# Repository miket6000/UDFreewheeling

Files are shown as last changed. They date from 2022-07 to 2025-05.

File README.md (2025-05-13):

# UDFreewheeling
A Freewheeling DRSSTC controller based loosely on the UD2.7. See it running my 35cm coil here: (https://youtu.be/EUlrq9CbajI)

Follow the development history at https://highvoltageforum.net/index.php?topic=2054.0

The driver behind building a new Tesla Coil Controller was to create something as simple to build and use as the UD2.7 (https://loneoceans.com/labs/ud27/) but with the below improvements:
* Freewheeling over current protection, this limits the maximum current without terminating the burst
* Over current and current phase detected with a single current transformer (CT)
* Removed the need for difficult to obtain variable inductors
* Self oscillating for improved startup at lower feedback currents

There are a couple of breaking changes that are worth pointing out:
* While the board outline is approximately the same as UD2.7 I can't guarantee the mounting holes are in the exact same locations
* There is no longer the ability to disable phase lead, it wasn't obvious why this would be required and can be done by using a short instead of L1
* The location of the HFBR is approximately the same as the UD2.7 but the location of the IF-D95 has changed slightly

Huge thanks to the assistance of all those at highvoltageforum.net and especially David Knierim for his extensive contributions.

## How it works
### Power supply
There's nothing much here to talk about, there are three regulators, 24V, 9V and 5V. 24V and 5V are linear, the 9V should be a DC/DC converter such as  RECOM Power R-78E9.0-0.5 or similar. It is recommended for the input supply that you use a 1A 24V SMPS and the DC input. Do not use the DC and AC inputs at the same time.

### Phase detect
The CT should be designed to provide a current of ~500mA to 1A peak at maximum primary current.
C32 provides HF bypass for noise. The current from the CT passes through R3 || R8 L1 and R1 generating a voltage ton pin 1 of R8 hat leads the current by theta = arctan(Xl / R). Xl depends on the operating frequency of the primary but R just depends on the position of the wiper on R8 and can be set from 5.1R up to R3 || R9 which is approximately 22R. This voltage is then clamped to +/- 0.65V by the back to back diodes and capacitvely coupled into the inverting input of the comparator IC8.

IC8 is set up with both positive and negative feedback with the non-inverting input held at nominally 2.5V. If we initially ignore any input from the CT we can see that the comparator will attempt to pull the inverting input low. There will be a time constant set by C5 and (R21 + R25) which will mean this takes some amount of time but the voltage at the input will be reducing. Meanwhile when the input transitioned low C33, R26 and R7 immediately pulled the non-inverting input low but C33 will slowly charge so the voltage at the non-inverting input will be increasing.

After some amount of time the increasing voltage on the non-inverting input and the decreasing voltage in the inverting input will be equal and the pass each other. At this moment the comparator will toggle states at the output will go high. This will reverse our initial state and everything happens again, but with the voltages reversed, i.e. it oscillates. The oscillation frequency can be set by adjusting R25. This should be set as close as possible to the frequency of the primary. To set the correct frequency ensure there is no feedback from the CT (i.e. disconnect the output stage or the CT) and measure the frequency on an oscilloscope. Adjust R25 until this matches your expected resonant frequency.

When there is a signal from the CT it swamps the ability of the negative feedback from R21 + R25 to control the inverting input pin so is effectively overriden with the natural resonant frequency of the system.

### Over current detection
The current through the CT creates a voltage across R1 (5R1). This is clamped between the 0V and 5V rails and feed into the inverting input of U5A. If the voltage exceeds the voltage set by R20 then the output of the comparator will go low signaling an over current event to the logic controlling the gate drivers. The over current threshold is determined by taking your intended over current peak, dividing it by the CT ratio and multiplying by 5.1V. R20 is then adjusted until this voltage is measured on TP6. E.G. I have a 300:1 CT and want the over current limit to be set to 200A, so I adjust R20 until I see 200A / 300 * 5.1V = 3.4V.

### Interrupt input
A signal present on the optical input of RX1 (active low) is inverted by IC4F so that the output is high when the signal is present (LED on). A signal present on the optical input of RX2 (active high) is first inverted and the pulls down the same node as RX1 which is then inverted again so that the output is again high when the signal is present. The two RX inputs are effectively OR'd together so it is not recommended to use both inputs at the same time. If RX2 is not placed it is necessary to either tie the input of IC4B low (by shorting RX2-RX1) or remove D12. Note, if you do decide to remove D12 it is still necessary to include R11 to prevent oscillation caused by a floating input to IC4B.

### Undervoltage Lockout (UVLO)
The under voltage lockout compares the 24V rail (divided by 6 and applied to the non-inverting input of U5B) to the reference voltage set by R27 applied to the inverting input of U5B. If the voltage drops below the reference voltage the output goes low signaling to the gate drive logic that an undervoltage has occured. The reference is set by dividing your desired UVLO voltage by 6 and adjusting R27 until you see the desired voltage on TP4. E.G. I want UVLO to trigger at 18V, 18V / 6 = 3V so I adjust R27 until I measure 3V on TP4.

### Gate drivers
This is borrowed directly from UD2.7C, the two UCC27423 dual inverting gate drivers are used to drive two FDD8424H complementry MOSFETs to run the gate drive transformers. The only difference is that there are seperate signals for the two GDTs. This means it is not possible to parallel the twou outputs, each needs to run its own GDT, one for each half of the full bridge. 

### Gate drive logic
This is the complex part. We'll start at the gate drivers and move backwards...
IC12 is a multiplexer. It has two sets of 4 inputs and will take one of the two sets of inputs and connect them to the outputs. The schematic uses a slightly different nomenclature than the datasheet but for each pair of input pins ('I0a' & 'I1a' are one pair) if the 'S' pin is low then the voltage at input 'I0a' is connected to output 'Za', if the 'S' pin is high then the voltage at 'I1a' is connected to 'Za'. All the pairs are switched at the same time. This is all assuming the Enable (E) pin is low, otherwise the outputs are all low.

We connect CLK to our 'S' pin. Looking at the 'a' and 'b' inputs which connect to GDT1 we can see that 'Za' and 'Zb' have complementy outputs, if 'Za' is high, 'Zb' is low and vice-verse. CLK is derived from our phase signal so always drives GDT1 in phase with the phase signal. Inputs 'c' and 'd' are more complex. They are driven by the putpus of IC6B so depending on the state of IC6B could be either driven in phase or out of phase with CLK. If they're driven in phase with CLK (i.e. 'Q' is high) then both sides of the H-bridge will be in phase with each other and there will be no voltage across the primary tank circuit, i.e. we're freewheeling. The currents in the LC circuit are free to slosh backwards and forwards without significant resistance from the bridge. If however 'Q' is low then the output to GDT2 is out of phase and the HVDC bus voltage will occure across the primary tank causing it to ring up.

IC6B samples IC6A's 'Qn' output and latches it for the next clock cycle on every rising 'CLK' edge. Under "normal" circumstances IC6A clocks in 5V on the 'D' pin so 'Qn' is 0V. 0V on the 'D' pin of IC6B means the drive is out of phase and we ring up the current. If however OCD is asserted low by the over current detect comparator at any stage during the clock cycle the output of IC6B's 'Qn' output will go high. It will stay high until the next clock edge samples the 'D' input and drives 'Qn' low again, but going low takes time, before that happens the state has already been samples by IC6B and locked in for the next cycle. The INTERRUPT signal on the 'set' pin just ensures that we're in the correct state (freewheeling off) in between on signals from the interrupter, otherwise we wouldn't be able to start.

IC5A will disable the output of IC12 whenever INTERRUPT is low and there is a rising edge on the CLK signal. It can also disable IC12 if its 'R' line is asserted low by IC5B which is used to latch the UVLO signal. This means that if the UVLO is triggered then the output will remain locked out until the next rising edge of INTERRUPT.

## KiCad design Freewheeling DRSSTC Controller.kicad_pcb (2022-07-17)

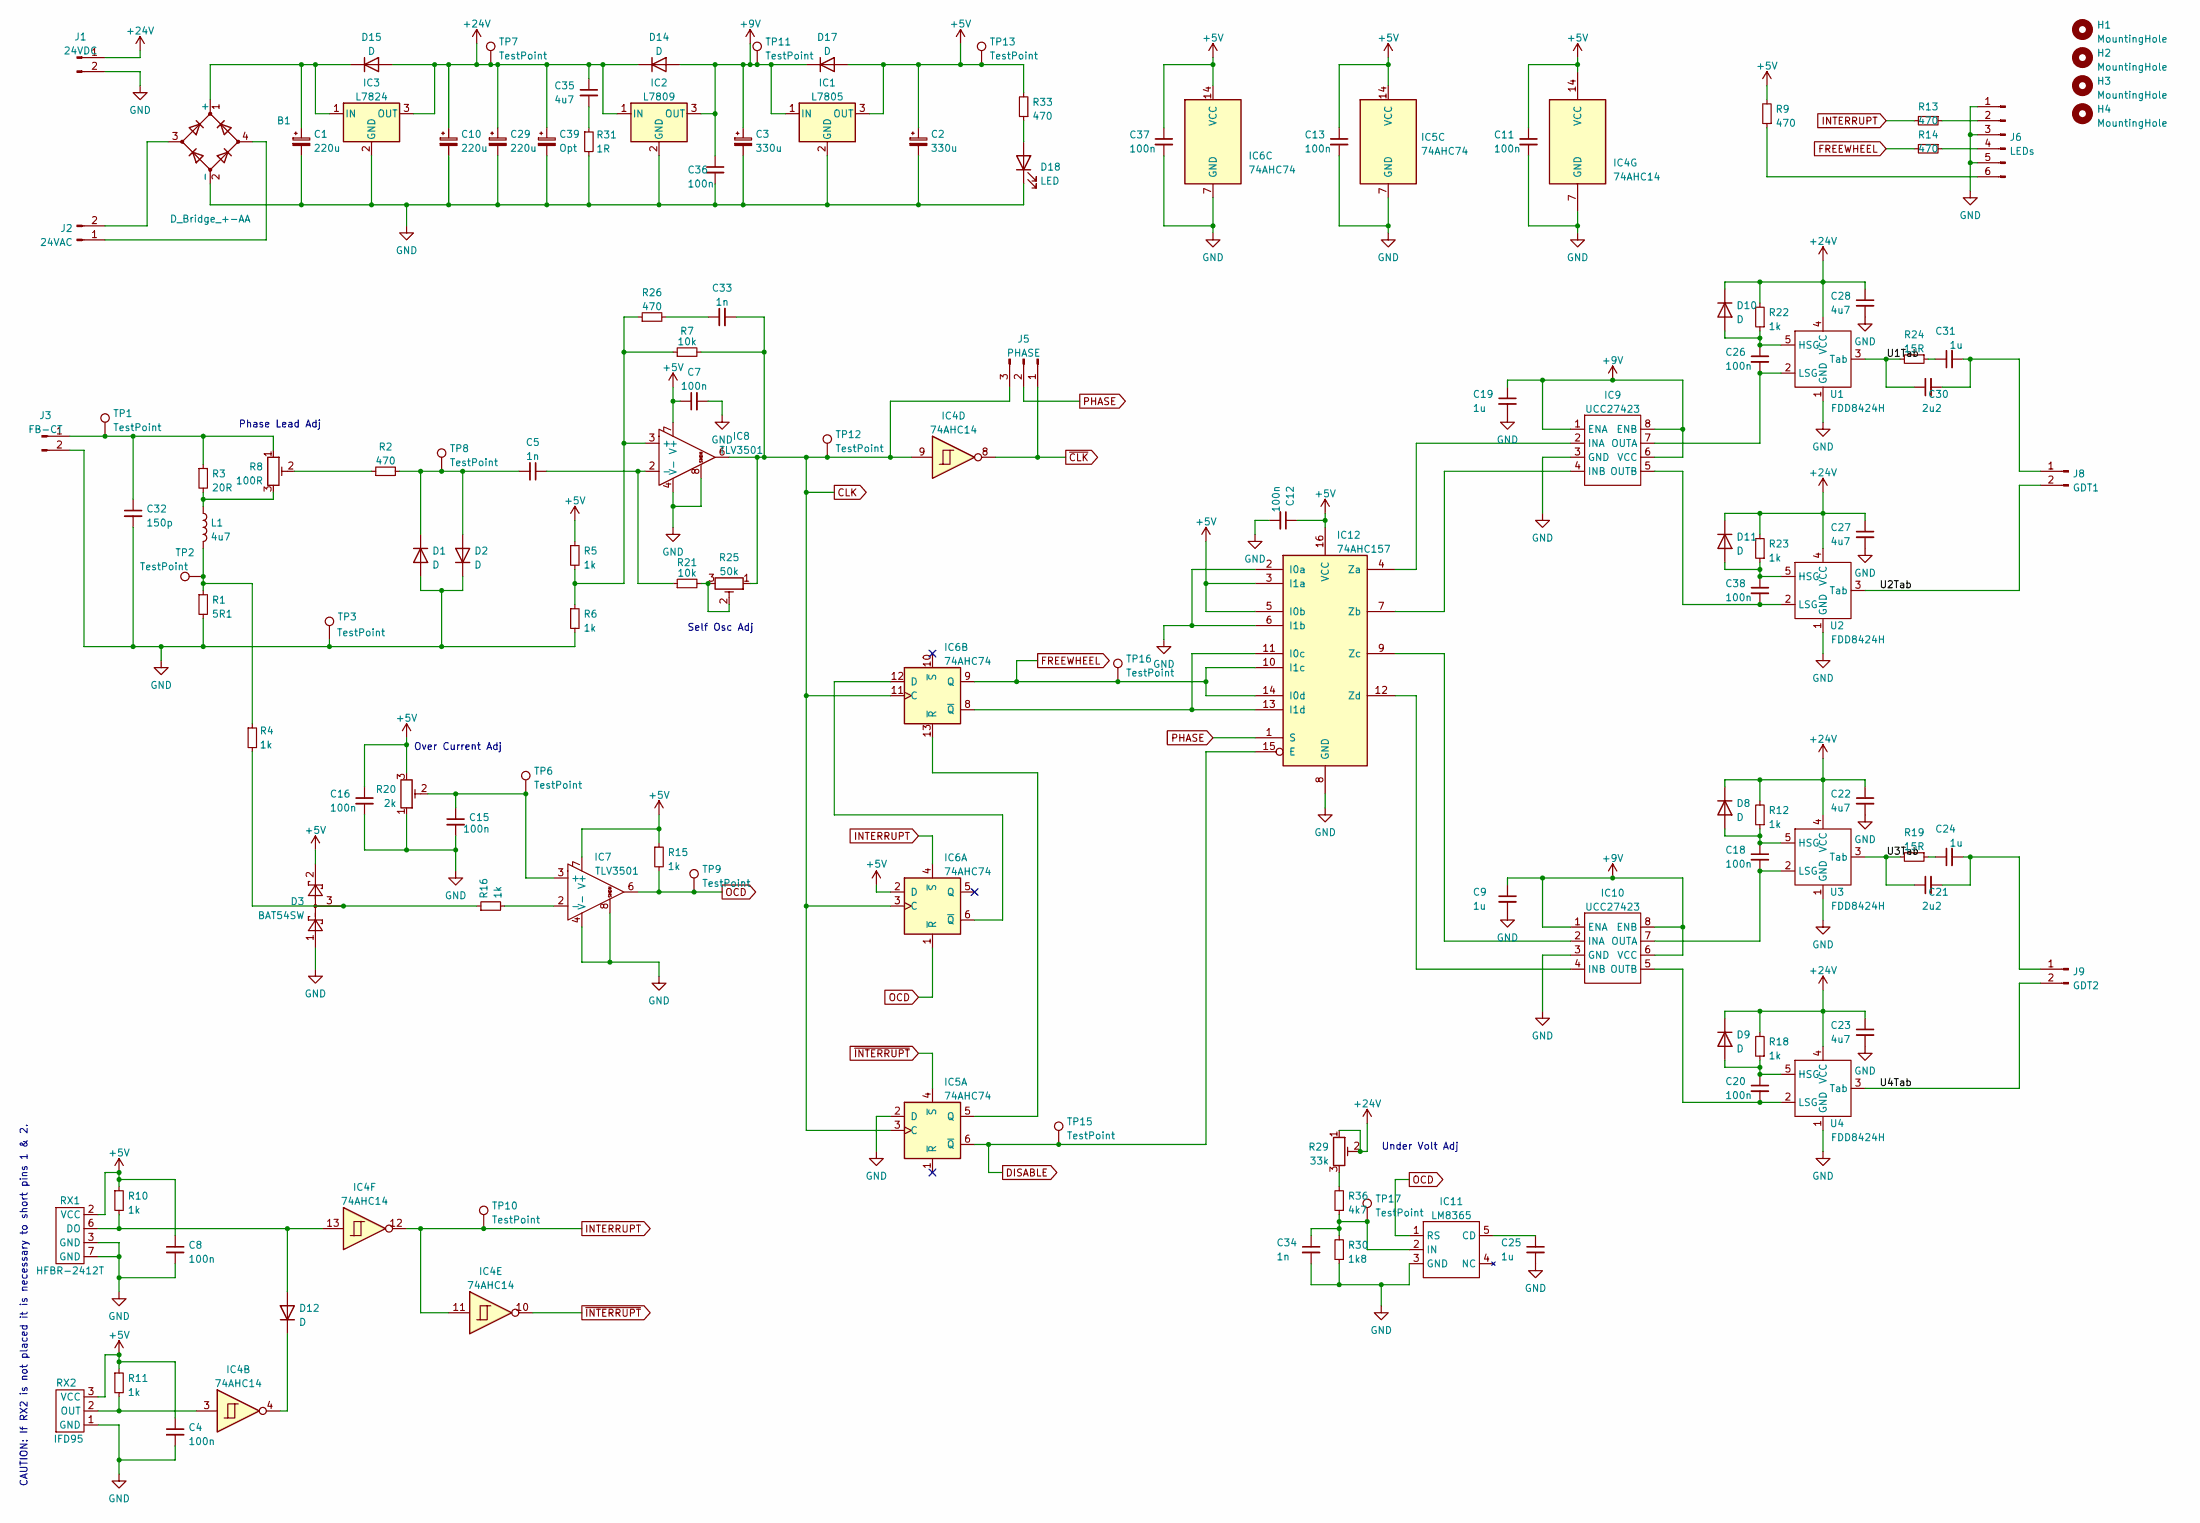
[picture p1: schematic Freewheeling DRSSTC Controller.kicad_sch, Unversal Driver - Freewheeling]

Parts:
B1: D_Bridge_+-AA; Diode_Bridge_Vishay_DFS
C1, C10, C29: 220u; CP_Radial_D8.0mm_P3.50mm
C2, C3: 330u; CP_Radial_D8.0mm_P3.50mm
C4, C7, C8, C11, C12, C13, C15, C16, C18, C20, C26, C36, C37, C38: 100n; C_0805_2012Metric
C5, C33, C34: 1n; C_0805_2012Metric
C9, C19, C25: 1u; C_0805_2012Metric
C21, C30: 2u2; C_1210_3225Metric
C22, C23, C27, C28, C35: 4u7; C_1206_3216Metric
C24, C31: 1u; C_1206_3216Metric
C32: 150p; C_0805_2012Metric
C39: Opt; CP_Radial_D8.0mm_P3.50mm
D1, D2, D14, D15, D17: D; D_SOD-123
D3: BAT54SW; SOT-23
D8, D9, D10, D11, D12: D; D_SOD-323
D18: LED; D_0805_2012Metric
H1, H2, H3, H4: MountingHole; MountingHole_3.2mm_M3
IC1: L7805; TO-252-3_TabPin2
IC2: L7809; TO-220-3_Vertical
IC3: L7824; TO-263-2
IC4: 74AHC14; SOIC-14_3.9x8.7mm_P1.27mm
IC5, IC6: 74AHC74; SOIC-14_3.9x8.7mm_P1.27mm
IC7, IC8: TLV3501; SOIC-8_3.9x4.9mm_P1.27mm
IC9, IC10: UCC27423; SOIC-8_3.9x4.9mm_P1.27mm
IC11: LM8365; SOT-23-5
IC12: 74AHC157; SOIC-16_3.9x9.9mm_P1.27mm
J1: 24VDC; JST_XH_B2B-XH-A_1x02_P2.50mm_Vertical
J2: 24VAC; JST_XH_B2B-XH-A_1x02_P2.50mm_Vertical
J3: FB-CT; JST_XH_B2B-XH-A_1x02_P2.50mm_Vertical
J5: PHASE; PinHeader_1x03_P2.54mm_Vertical
J6: LEDs; PinHeader_1x06_P2.54mm_Vertical
J8: GDT1; JST_XH_B2B-XH-A_1x02_P2.50mm_Vertical
J9: GDT2; JST_XH_B2B-XH-A_1x02_P2.50mm_Vertical
L1: 4u7; L_Axial_L11.0mm_D4.5mm_P5.08mm_Vertical_Fastron_MECC
R1: 5R1; R_Axial_DIN0414_L11.9mm_D4.5mm_P15.24mm_Horizontal
R2, R9, R13, R14, R26, R33: 470; R_0805_2012Metric
R3: 20R; R_Axial_DIN0414_L11.9mm_D4.5mm_P15.24mm_Horizontal
R4, R5, R6, R10, R11, R12, R15, R16, R18, R22, R23: 1k; R_0805_2012Metric
R7, R21: 10k; R_0805_2012Metric
R8: 100R; Potentiometer_Bourns_3296W_Vertical
R19, R24: 15R; R_1210_3225Metric
R20: 2k; Potentiometer_Bourns_3296W_Vertical
R25: 50k; Potentiometer_Bourns_3296W_Vertical
R29: 33k; Potentiometer_Bourns_TC33X_Vertical
R30: 1k8; R_0805_2012Metric
R31: 1R; R_0805_2012Metric
R36: 4k7; R_0805_2012Metric
RX1: HFBR-2412T; HFBR-x41x
RX2: IFD95; IF-D95
TP1, TP2, TP3, TP6, TP7, TP8, TP9, TP10, TP11, TP12, TP13, TP15, TP16, TP17: TestPoint; TestPoint_THTPad_D1.0mm_Drill0.5mm
U1, U2, U3, U4: FDD8424H; TO-252-4

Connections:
+5V: C2.1, C4.1, C7.1, C8.1, C11.1, C12.1, C13.1, C16.1, C37.1, D3.2, D17.2 (A), IC1.3 (OUT), IC4.14 (VCC), IC5.14 (VCC), IC6.2 (D), IC6.14 (VCC), IC7.7 (V+), IC8.7 (V+), IC12.3 (I1a), IC12.5 (I0b), IC12.16 (VCC), R5.1, R9.2, R10.1, R11.1, R15.1, R20.3, R33.2, RX1.2 (VCC), RX2.3 (VCC), TP13.1
+9V: C3.1, C9.1, C19.1, C36.1, D14.2 (A), D17.1 (K), IC1.1 (IN), IC2.3 (OUT), IC9.1 (ENA), IC9.6 (VCC), IC9.8 (ENB), IC10.1 (ENA), IC10.6 (VCC), IC10.8 (ENB), TP11.1
+24V: C10.1, C22.1, C23.1, C27.1, C28.1, C29.1, C35.1, C39.1, D8.1 (K), D9.1 (K), D10.1 (K), D11.1 (K), D14.1 (K), D15.2 (A), IC2.1 (IN), IC3.3 (OUT), J1.1, R12.2, R18.2, R22.2, R23.2, R29.1, R29.2, TP7.1, U1.4 (VCC), U2.4 (VCC), U3.4 (VCC), U4.4 (VCC)
/U1Tab: C30.1, R24.2, U1.3 (Tab)
/U2Tab: J8.2, U2.3 (Tab)
/U3Tab: C21.1, R19.2, U3.3 (Tab)
/U4Tab: J9.2, U4.3 (Tab)
CLK: C33.2, IC4.9, IC5.3 (C), IC6.3 (C), IC6.11 (C), IC8.6, J5.3, R7.2, R25.1, TP12.1
DISABLE: IC5.6 (~Q), IC12.15 (E), TP15.1
FREEWHEEL: IC6.9 (Q), IC12.10 (I1c), IC12.14 (I0d), R14.2, TP16.1
GND: B1.2 (-), C1.2, C2.2, C3.2, C4.2, C7.2, C8.2, C9.2, C10.2, C11.2, C12.2, C13.2, C15.2, C16.2, C19.2, C22.2, C23.2, C25.2, C27.2, C28.2, C29.2, C32.2, C34.2, C36.2, C37.2, C39.2, D1.2 (A), D2.1 (K), D3.1, D18.1 (K), IC1.2 (GND), IC2.2 (GND), IC3.2 (GND), IC4.7 (GND), IC5.2 (D), IC5.7 (GND), IC6.7 (GND), IC7.4 (V-), IC7.8, IC8.4 (V-), IC8.8, IC9.3 (GND), IC10.3 (GND), IC11.3 (GND), IC12.2 (I0a), IC12.6 (I1b), IC12.8 (GND), J1.2, J3.2, J6.1, J6.3, J6.5, R1.2, R6.2, R20.1, R30.1, R31.2, RX1.3 (GND), RX1.7 (GND), RX2.1 (GND), TP3.1, U1.1 (GND), U2.1 (GND), U3.1 (GND), U4.1 (GND)
INTERRUPT: IC4.11, IC4.12, IC6.4 (~S), R13.2, TP10.1
unnamed: B1.1 (+), C1.1, D15.1 (K), IC3.1 (IN)
unnamed: B1.3, J2.2
unnamed: B1.4, J2.1
unnamed: C18.1, D8.2 (A), R12.1, U3.5 (HSG)
unnamed: C18.2, IC10.7 (OUTA), U3.2 (LSG)
unnamed: C20.1, D9.2 (A), R18.1, U4.5 (HSG)
unnamed: C20.2, IC10.5 (OUTB), U4.2 (LSG)
unnamed: C21.2, C24.2, J9.1
unnamed: C24.1, R19.1
unnamed: C25.1, IC11.5 (CD)
unnamed: C26.1, D10.2 (A), R22.1, U1.5 (HSG)
unnamed: C26.2, IC9.7 (OUTA), U1.2 (LSG)
unnamed: C30.2, C31.2, J8.1
unnamed: C31.1, R24.1
unnamed: C33.1, R26.2
unnamed: C34.1, IC11.2 (IN), R30.2, R36.1, TP17.1
unnamed: C35.2, R31.1
unnamed: C38.1, D11.2 (A), R23.1, U2.5 (HSG)
unnamed: C38.2, IC9.5 (OUTB), U2.2 (LSG)
unnamed: C5.2, D1.1 (K), D2.2 (A), R2.2, TP8.1
unnamed: D12.1 (K), IC4.4
unnamed: D12.2 (A), IC4.13, R10.2, RX1.6 (DO)
unnamed: D18.2 (A), R33.1
unnamed: IC4.3, R11.2, RX2.2 (OUT)
unnamed: IC6.8 (~Q), IC12.11 (I0c), IC12.13 (I1d)
unnamed: IC6.6 (~Q), IC6.12 (D)
unnamed: IC5.5 (Q), IC6.13 (~R)
unnamed: IC7.2 (-), R16.2
unnamed: C5.1, IC8.2 (-), R21.1
unnamed: IC9.2 (INA), IC12.4 (Za)
unnamed: IC9.4 (INB), IC12.7 (Zb)
unnamed: IC10.2 (INA), IC12.9 (Zc)
unnamed: IC10.4 (INB), IC12.12 (Zd)
unnamed: J6.2, R13.1
unnamed: J6.4, R14.1
unnamed: J6.6, R9.1
unnamed: L1.1, R3.2, R8.3
unnamed: L1.2, R1.1, R4.1, TP2.1
unnamed: C32.1, J3.1, R3.1, R8.1, TP1.1
unnamed: R2.1, R8.2
unnamed: D3.3, R4.2, R16.1
unnamed: C15.1, IC7.3 (+), R20.2, TP6.1
unnamed: R21.2, R25.2, R25.3
unnamed: IC8.3 (+), R5.2, R6.1, R7.1, R26.1
unnamed: R29.3, R36.2
OCD: IC6.1 (~R), IC7.6, IC11.1 (RS), R15.2, TP9.1
PHASE: IC12.1 (S), J5.2
~CLK: IC4.8, J5.1
~INTERRUPT: IC4.10, IC5.4 (~S)

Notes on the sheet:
CAUTION: If RX2 is not placed it is necessary to short pins 1 & 2.
Over Current Adj
Under Volt Adj
Self Osc Adj
Phase Lead Adj

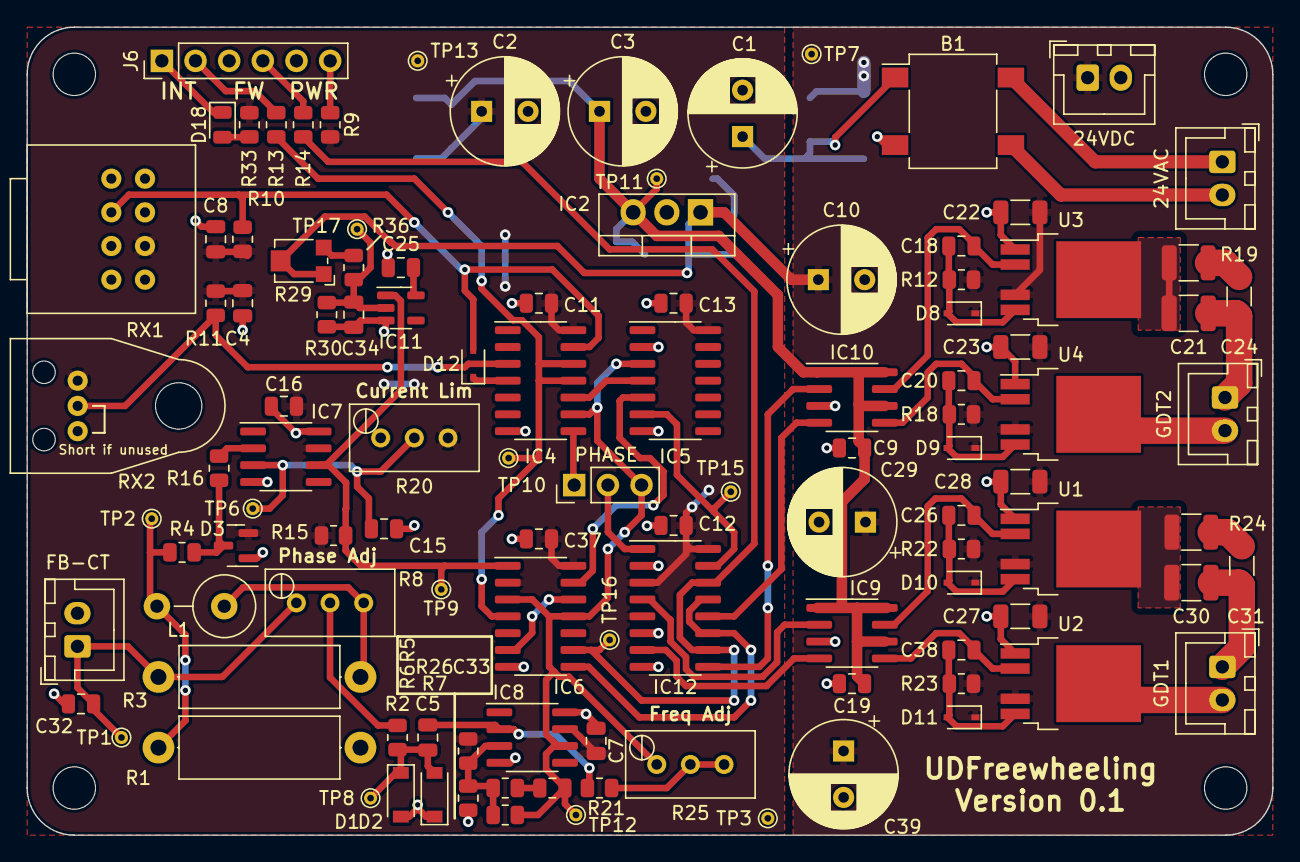
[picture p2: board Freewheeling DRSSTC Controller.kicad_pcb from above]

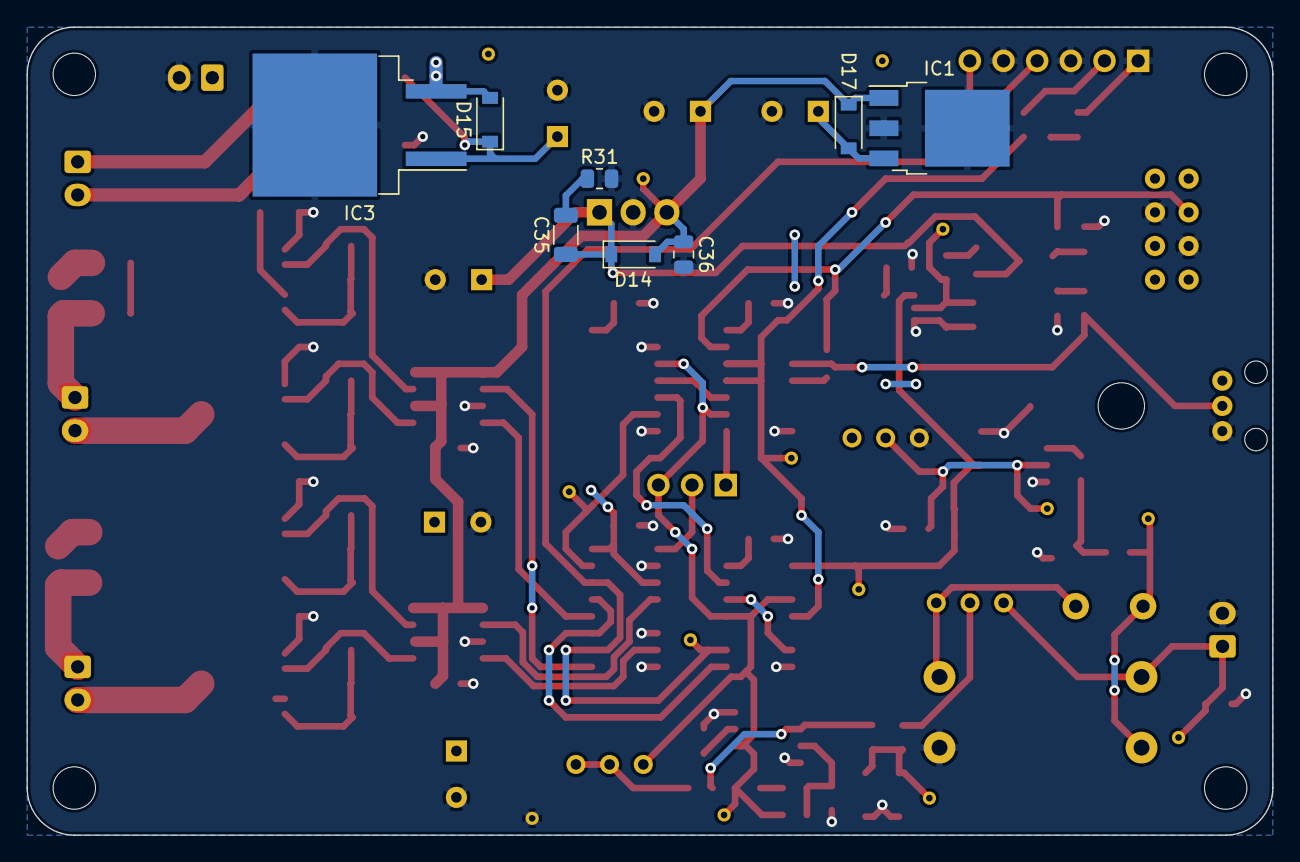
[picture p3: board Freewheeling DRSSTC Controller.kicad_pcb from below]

Board: 2 copper layers, 94.0 x 61.0 mm, 123 parts (8 on the bottom side), 61 nets.
